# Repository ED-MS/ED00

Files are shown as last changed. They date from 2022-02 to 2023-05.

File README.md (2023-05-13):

# ED00 Labeler

## Manual milk labeler, designed by EDMS ([web site](https://www.ed-ms.fr))

*If you think this design is useful, do not hesitate to **donate** :wink:, see [company web site](https://www.ed-ms.fr) for that, thanks :+1:*

*If you find some mistakes or improvement on this design :monocle_face:, please create an **Issue** or a **Pull request** on this repository.*

This repository contains :
- STL files of 3D printed parts
- image files of 3D printed part
- PDF 3D file to see where each part is located

## 3D printed parts
- Total of ~1kg of plastic filament required
- ~60 hours of printing in total (using a PRUSA MK3S printer)
- Minimum printing volume requested : 240mm x 205mm x 152mm

### 3D printing recommended parameters
- Material : PETG
- Layers height : 0.3mm
- Part filling : 20%
- No suppport required (except on 001001)

### Update 28th March 2023 : add design alternative (ED00-1) :
With initial design (ED00), labels gluing with milk is possible but it is a quite long process (it is necessary to turn very slowly). Labels gluing with glue is also possible (and quicker) but it is difficult to move the label after gluing.
With alternative design (ED00-1), labels gluing with milk is not possible but labels gluing with glue is very quick and it is possible to move the labels after gluing (to align it).

### 3D printing parts
| N° | Reference  |Image | Qty ED00 | Qty ED00-1 |
| -- | --- | --- | --- | --- |
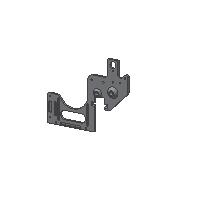
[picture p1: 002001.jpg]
| 1  | 002001 |  | 1 | 1 |
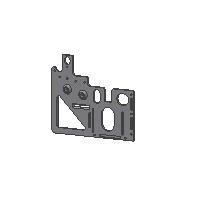
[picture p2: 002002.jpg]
| 2  | 002002 |  | 1 | 0 |
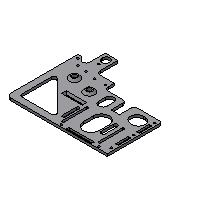
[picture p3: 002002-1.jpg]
| 2  | 002002-1 || 0 | 1 |
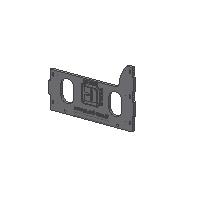
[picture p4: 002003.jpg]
| 3  | 002003 |  | 1 | 1 |
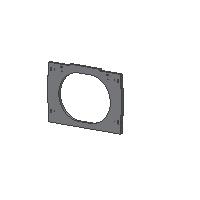
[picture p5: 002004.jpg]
| 4  | 002004 |  | 1 | 1 |
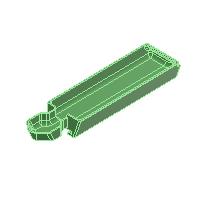
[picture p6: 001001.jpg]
| 5  | 001001 |  | 1 | 1 |
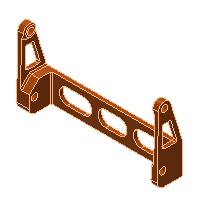
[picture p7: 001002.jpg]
| 6  | 001002 |  | 1 | 1 |
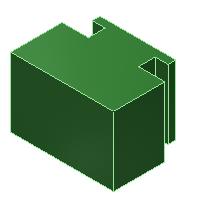
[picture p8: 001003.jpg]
| 7  | 001003 |  | 1 | 1 |
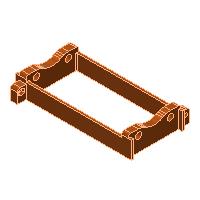
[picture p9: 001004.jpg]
| 8  | 001004 |  | 1 | 1 |
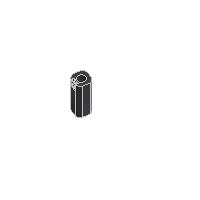
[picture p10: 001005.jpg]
| 9  | 001005 |  | 1 | 1 |
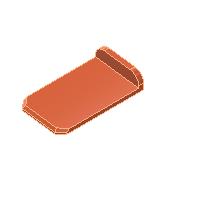
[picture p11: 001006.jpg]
| 10 | 001006 |  | 2 | 2 |
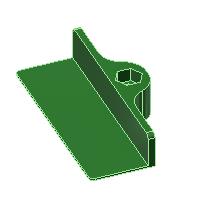
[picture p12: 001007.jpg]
| 11 | 001007 |  | 2 | 2 |
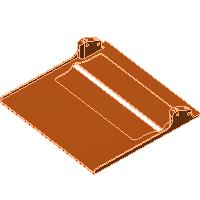
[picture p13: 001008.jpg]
| 12 | 001008 |  | 1 | 1 |
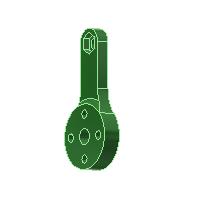
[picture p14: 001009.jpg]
| 13 | 001009 |  | 1 | 1 |
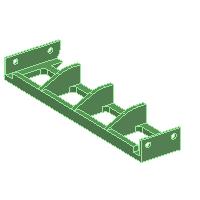
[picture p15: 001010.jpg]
| 14 | 001010 |  | 1 | 0 |
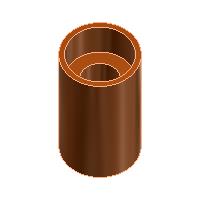
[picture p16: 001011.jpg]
| 15 | 001011 |  | 1 | 1 |
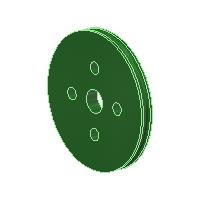
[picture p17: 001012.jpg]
| 16 | 001012 |  | 1 | 0 |
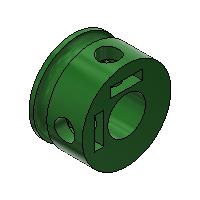
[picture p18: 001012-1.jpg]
| 17 | 001012-1 || 0 | 1 |
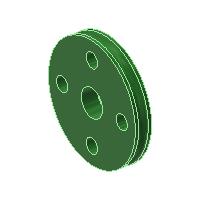
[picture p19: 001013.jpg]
| 18 | 001013 |  | 2 | 0 |
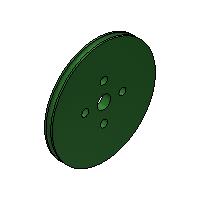
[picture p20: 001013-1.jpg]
| 19 | 001013-1 || 0 | 3 |
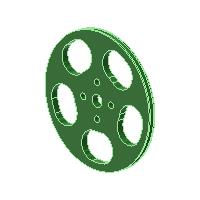
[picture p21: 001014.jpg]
| 20 | 001014 |  | 1 | 0 |
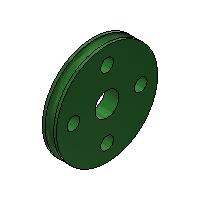
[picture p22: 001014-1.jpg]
| 21 | 001014-1 || 0 | 1 |
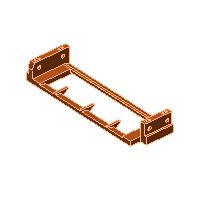
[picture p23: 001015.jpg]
| 22 | 001015 |  | 1 | 0 |
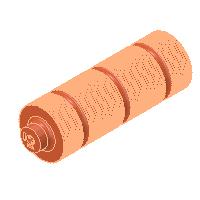
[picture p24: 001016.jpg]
| 23 | 001016 |  | 1 | 0 |
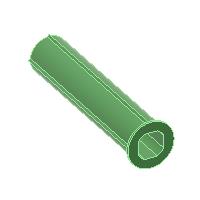
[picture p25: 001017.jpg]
| 24 | 001017 |  | 1 | 1 |
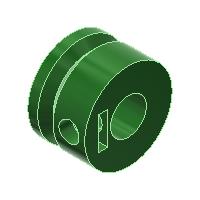
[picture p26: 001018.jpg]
| 25 | 001018 |  | 4 | 4 |
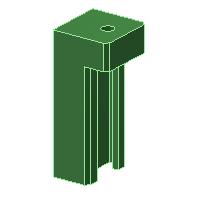
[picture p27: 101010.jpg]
| 26 | 101010 |  | 2 | 2 |
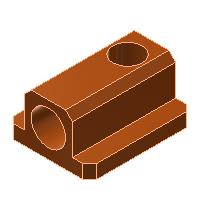
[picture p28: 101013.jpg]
| 27 | 101013 |  | 2 | 2 |
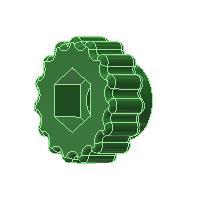
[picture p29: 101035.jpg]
| 28 | 101035 |  | 6 | 6 |
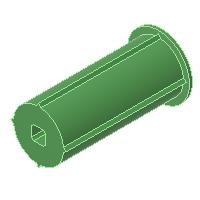
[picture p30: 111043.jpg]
| 29 | 111043 |  | 1 | 1 |
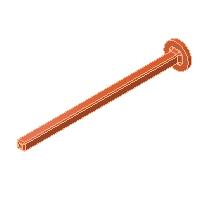
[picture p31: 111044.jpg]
| 30 | 111044 |  | 1 | 1 |
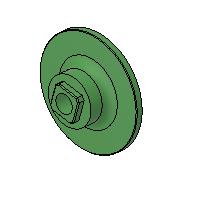
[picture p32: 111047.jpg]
| 31 | 111047 |  | 0 | 7 |
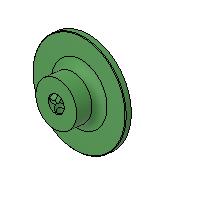
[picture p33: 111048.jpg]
| 32 | 111048 |  | 0 | 1 |
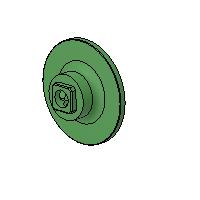
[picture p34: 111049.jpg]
| 33 | 111049 |  | 0 | 1 |
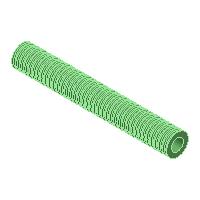
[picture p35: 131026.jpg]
| 34 | 131026 |  | 1 | 1 |
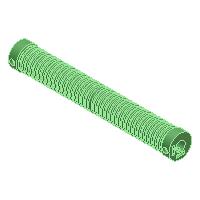
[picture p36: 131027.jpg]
| 35 | 131027 |  | 1 | 1 |
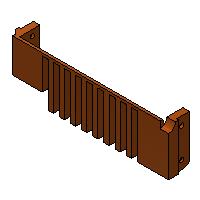
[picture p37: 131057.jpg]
| 36 | 131057 |  | 0 | 1 |
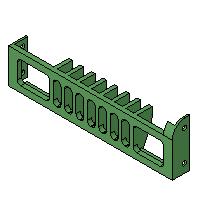
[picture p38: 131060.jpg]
| 37 | 131060 |  | 0 | 1 |

### Other parts
| N° | Designation | Qty ED00 | Qty ED00-1 | Proposed supplier | Note |
| -- | --- | --- | --- | --- | ---|
| 1  | Hex socket button head, flanged screw M4x16 | 29 | 25 | www.visseriefixations.fr/ | |
| 2  | Hex socket button head, screw | 4x M4x30 | 4x M4x35 | www.visseriefixations.fr/ |for 1009 |
| 3  | Headless, hex socket screw M4x6 | 11 | 13 | www.visseriefixations.fr/ | |
| 4  | Hex head screw M6x30 | 4 | 4 | www.visseriefixations.fr/ | |
| 5  | Hex head screw M6x45 | 3 | 3 | www.visseriefixations.fr/ | |
| 6  | Square nut M4x7x2 | 30 | 32 | www.visseriefixations.fr/ | |
| 7  | Self locking hex nut M4 | 16 | 12 | www.visseriefixations.fr/ | |
| 8  | Hex nut M6 | 8 | 8 | www.visseriefixations.fr/ | |
| 9  | Self locking hex nut M6 | 2 | 2 | www.visseriefixations.fr/ |for springs|
| 10 | Rigid flange coupling Ø8 | 3 | 2 | eBay or Aliexpress or www.ed-ms.fr | |
| 11 | Orange foam roll Ø45x25mm length 60mm | 3 | 3 | www.ed-ms.fr | |
| 12 | Spring Ø8.63mm ext, free length 40mm, wire diameter 0.63mm | 2 | 2 | fr.rs-online.com/web/ or www.ed-ms.fr |ref 751512 |
| 13 | Round belt Ø3mm PU weldable #1 | 220mm | 233mm | www.fiamag.com or www.ed-ms.fr | |
| 14 | Round belt Ø3mm PU weldable #2 | 410mm | 360mm | www.fiamag.com or www.ed-ms.fr | |
| 15 | Round belt Ø3mm PU weldable #3 | 0 | 350mm | www.fiamag.com or www.ed-ms.fr | |
| 16 | O Ring EPDM70 Ø15,47x3.53 | 78 | 78 | www.123roulement.com or www.ed-ms.fr  | |
| 17 | Flange ring IGUS GFM-0810-11 | 17 | 17 | www.igus.fr or www.ed-ms.fr | |
| 18 | Aluminium rod AWMP-08 or tube Ø8mm | 185mm x2 | 185mm x1 | www.igus.fr or www.ed-ms.fr | |
| 19 | Aluminium rod AWMP-08 or tube Ø8mm | 80mm x1  | 80mm x1 | www.igus.fr or www.ed-ms.fr | |
| 20 | Aluminium rod AWMP-08 or tube Ø8mm | 260mm x1 | 265mm x1 | www.igus.fr or www.ed-ms.fr | |
| 21 | Aluminium rod AWMP-08 or tube Ø8mm | 160mm x1 | 160mm x1 | www.igus.fr or www.ed-ms.fr | |
| 22 | Aluminium rod AWMP-08 or tube Ø8mm | 232mm x1 | 235mm x2 | www.igus.fr or www.ed-ms.fr | |
| 23 | Aluminium tube Ø8mm length 30mm | 1 | 1 | www.igus.fr or www.ed-ms.fr |for 1009 |
| 24 | Stainless steel axis Ø2.5mm length 130mm | 1 | 1 | www.igus.fr or www.ed-ms.fr |for 111044 |

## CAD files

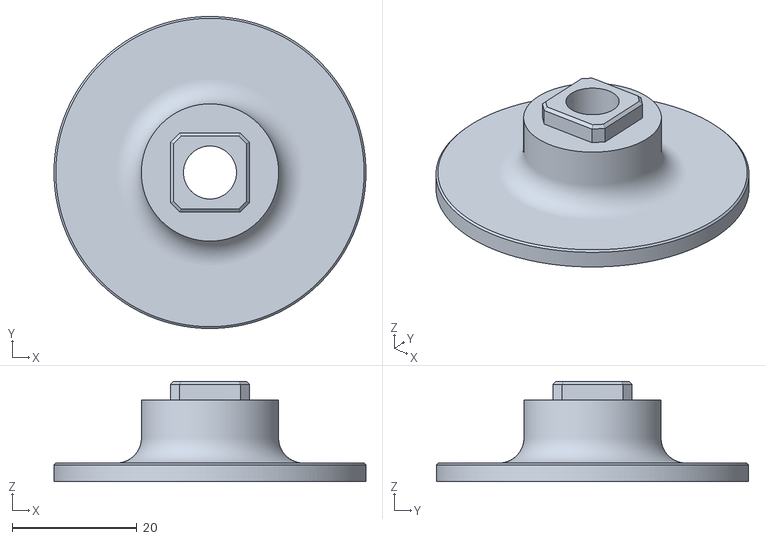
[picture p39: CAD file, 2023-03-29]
111047.stl
50.0 x 50.0 x 16.1

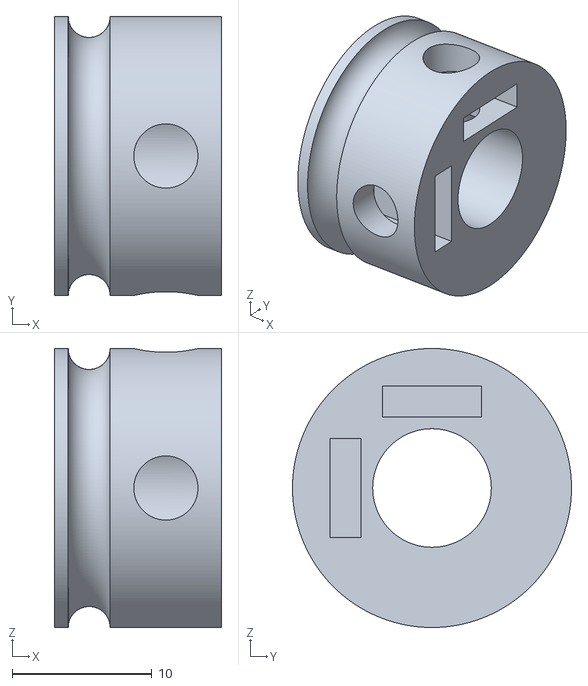
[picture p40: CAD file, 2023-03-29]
001012-1.stl
12.0 x 20.0 x 20.0

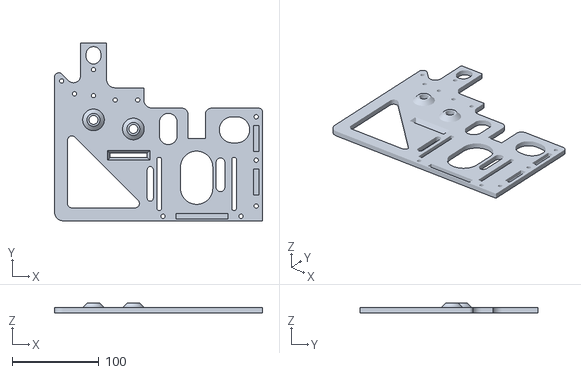
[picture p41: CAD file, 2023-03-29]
002002-1.stl
240.0 x 205.0 x 11.0

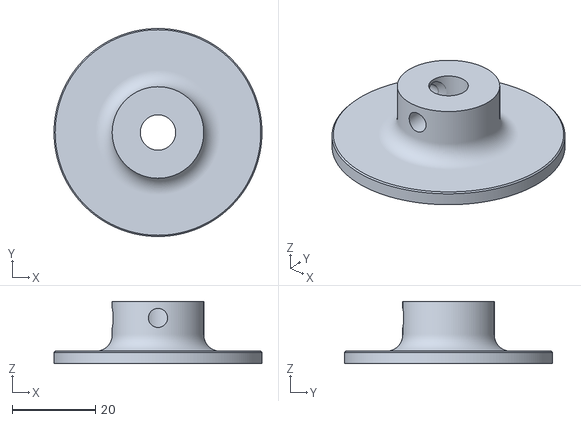
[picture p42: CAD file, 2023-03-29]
111048.stl
50.0 x 50.0 x 15.0

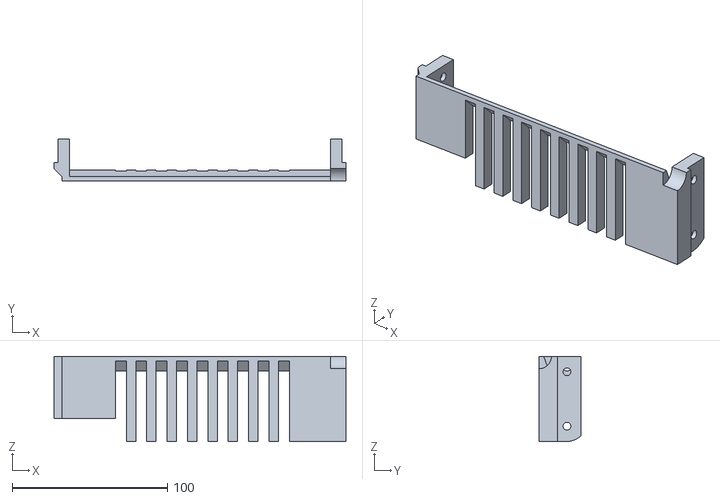
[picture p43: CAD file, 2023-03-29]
131057.stl
188.0 x 27.0 x 55.0

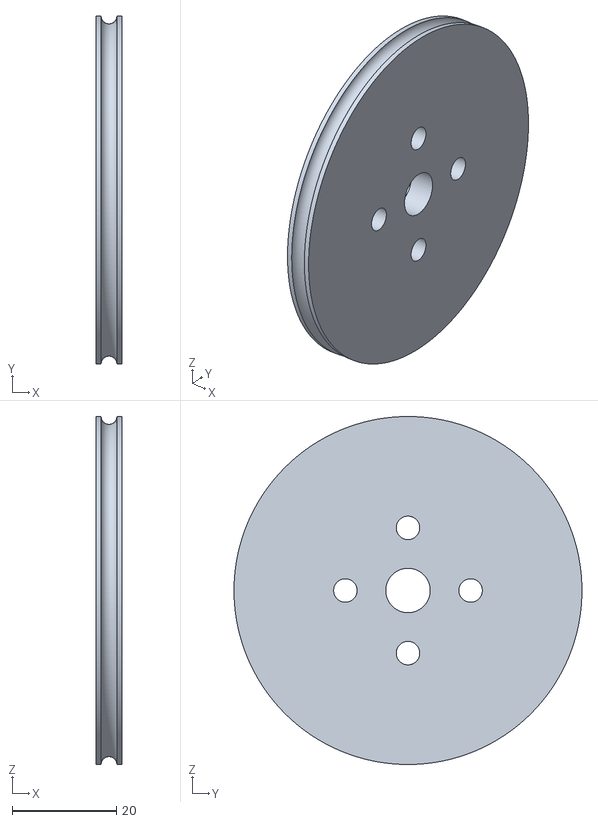
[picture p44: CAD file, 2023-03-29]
001013-1.stl
5.00 x 66.7 x 66.7

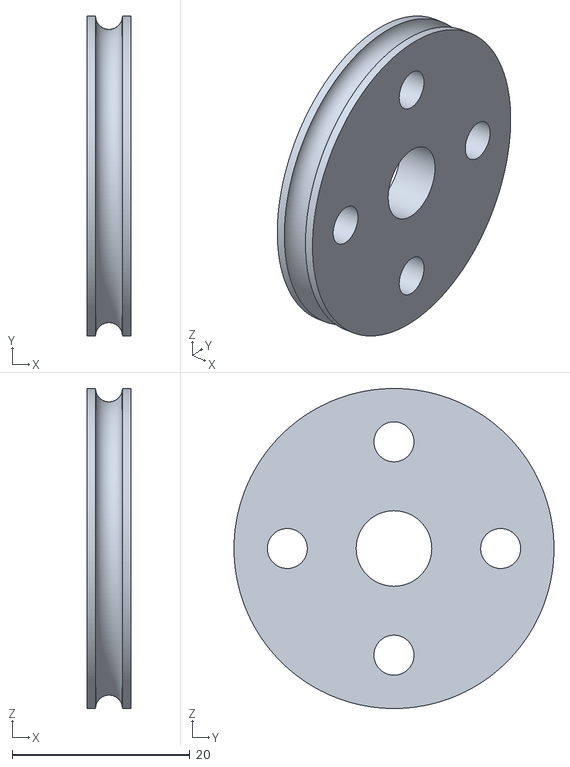
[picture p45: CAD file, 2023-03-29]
001014-1.stl
5.00 x 36.0 x 36.0

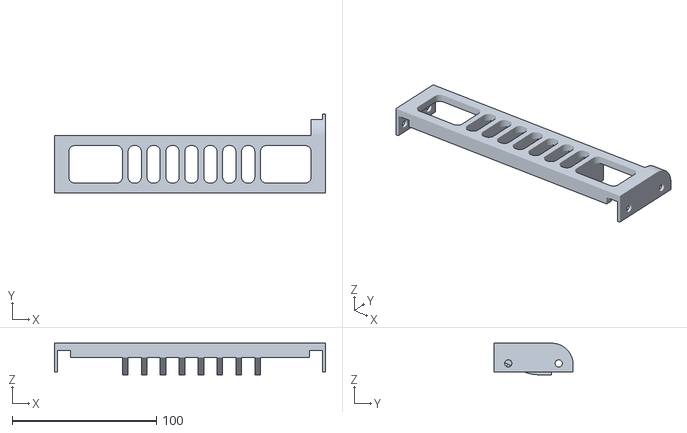
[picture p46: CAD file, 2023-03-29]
131060.stl
188.0 x 55.0 x 22.0

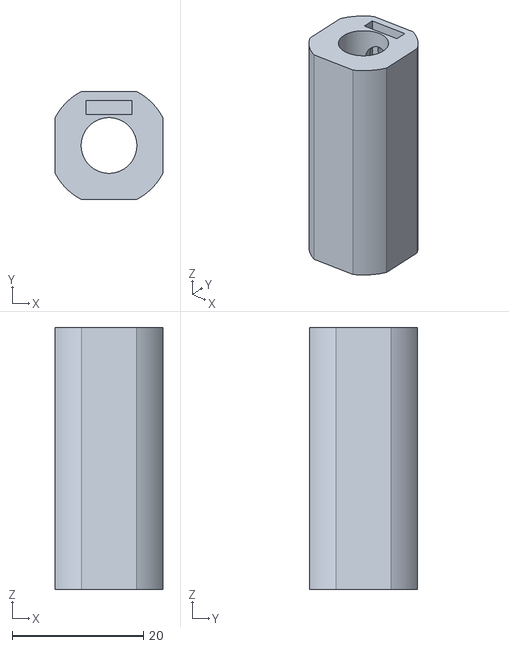
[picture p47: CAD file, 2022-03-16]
001005.stl
16.5 x 16.5 x 40.0

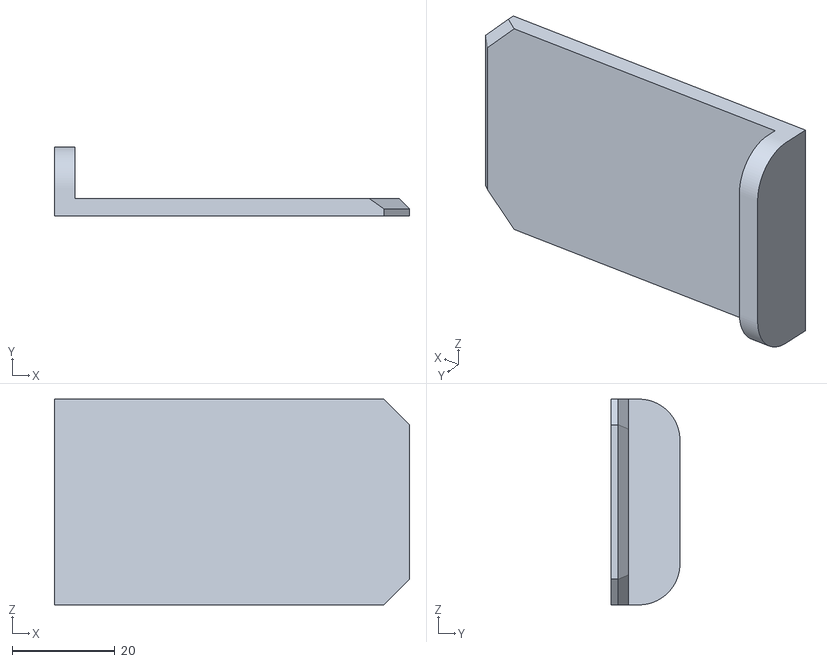
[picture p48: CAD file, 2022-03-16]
001006.stl
69.0 x 13.4 x 40.0

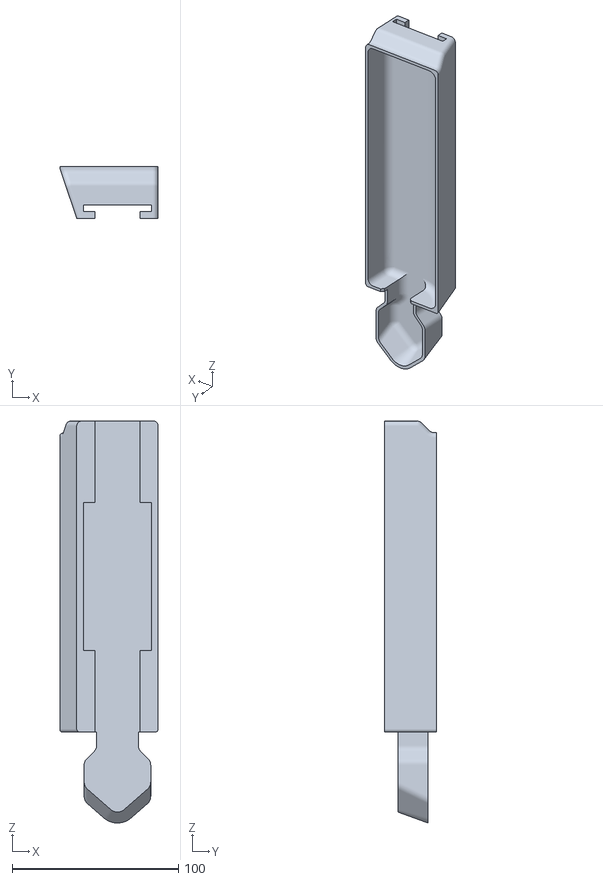
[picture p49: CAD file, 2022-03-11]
001001.stl
59.2 x 31.0 x 241.5

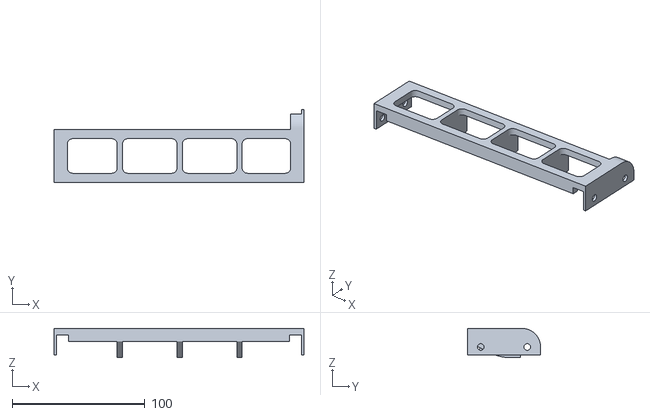
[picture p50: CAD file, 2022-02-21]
001010.stl
188.0 x 55.0 x 22.0

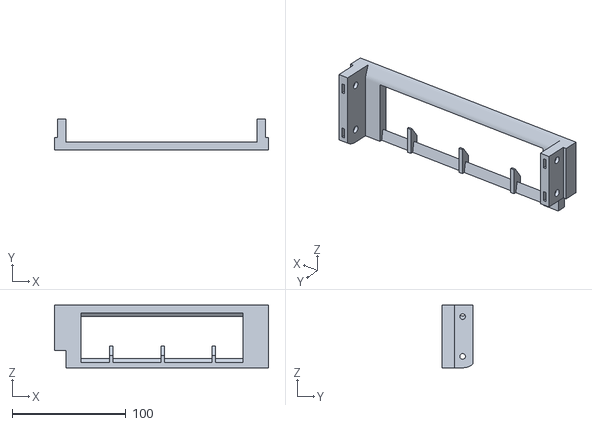
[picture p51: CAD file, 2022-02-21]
001015.stl
188.0 x 27.0 x 55.0

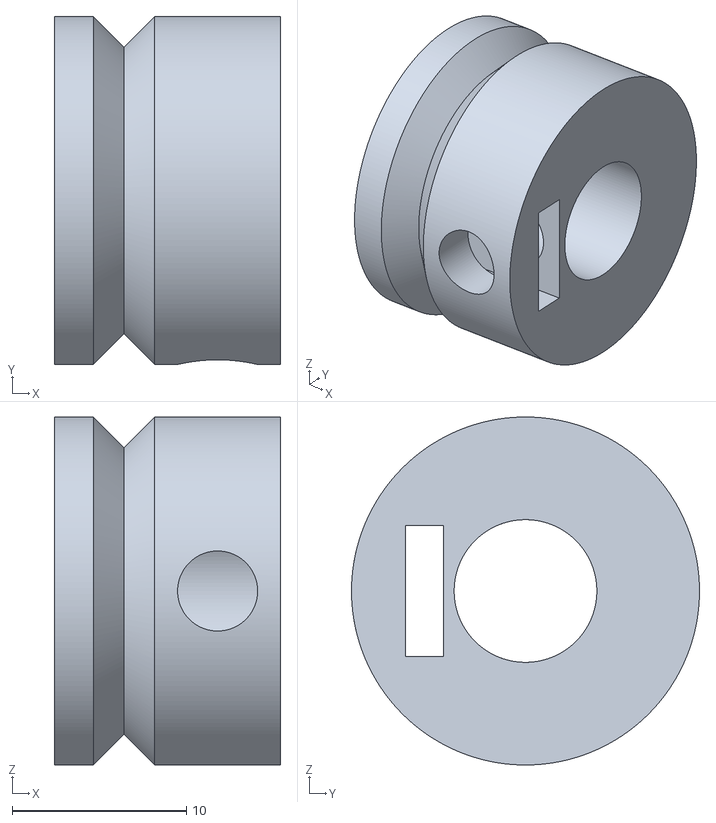
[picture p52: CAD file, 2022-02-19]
001018.stl
13.0 x 20.0 x 20.0

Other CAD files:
111049.stl
101013.stl
002001.stl
101035.stl
001002.stl
001003.stl
001004.stl
001007.stl
001008.stl
001009.stl
001011.stl
001012.stl
001013.stl
001014.stl
001017.stl
002002.stl
002003.stl
002004.stl
101010.stl
111043.stl
111044.stl
131026.stl
131027.stl

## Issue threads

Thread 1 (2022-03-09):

Correction erreurs

ericdaunay, 2022-03-09:
- [x] Manque 9 écrous carrés
- [x] Manque 4 Self locking hex nut M4
- [x] Consommation plastique :1kg
- [x] 185 plutot que 186mm
- [x] ajout axe de 2.5mm longueur 130mm
- [x] revoir l'embout carré
- [x] longueur courroie 1 : 221mm
- [x] longueur courroie 2 : 410mm
- [x] longueur tube 29 ald 26mm
- [x] ajouter un axe acier dia 2.5

ericdaunay, 2022-03-16:
all is done

Closed 2022-03-16.

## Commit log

2022-02-14 Ajout fichiers STL
    [001001.stl, 001002.stl, 001003.stl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]
2022-02-14 Ajout liste de pièces dans readme
2022-02-19 Change 001018 design
    [001018.stl]
2022-02-21 Add 1010 & 1015
    pour éviter que les étiquettes soient bloquées par moment
    [001010.stl, 001015.stl]
2022-03-11 Chamfer remove on 1010
    To make the printing easier
    [001001.stl]
2022-03-11 Assembly pictures
2022-03-16 Design improvement
    1005 : thickness increase for square nut resistance
    1006 : Thickness decrease
    1001 : chamfer removed for tightness
    [001005.stl, 001006.stl]
2022-03-16 Design improvement
    1006 : thicjness decreased
    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
2023-03-28 Add ED00-1
    [001012-1.stl, 001013-1.stl, 001014-1.stl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]
2023-05-13 Update README.md
    increase length of round belt from 220mm to 233mm
2023-05-17 File update due to mistake on round belt installation
